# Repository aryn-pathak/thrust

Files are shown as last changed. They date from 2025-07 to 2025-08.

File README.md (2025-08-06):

# THRUST Freestyle drone and FC

## THRUST is an open source, sleek, lightweight, entry level FPV freestyle drone, powered by the custom THRUST FC made from scratch.

### THE THRUST MK1:

**A high speed drone, in a minimalistic yet striking frame, built for agility and a comfortable flying feel.**






### THE THRUST FC:

**Built to beat inaccesible, expensive, and capitalist FCs, at almost 1/6th the price of an average commercial FC, with the same perfomance, based on STM32F401CCU6, package of 40x31mm.**

Screenshot 2025-08-06 at 5 40 20 PM
Screenshot 2025-07-30 at 11 06 15 PM
Screenshot 2025-07-30 at 11 09 15 PM

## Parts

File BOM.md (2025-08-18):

# FC COMPONENTS

| Item | Price (INR) | Price (USD) |
| --- | --- | --- |
| [STM32F401CCU6](https://robu.in/product/stm32f401ccu6-stmicroelectronics-stm32f401ccu6-arm-mcu-dynamic-efficiency-line-stm32-family-stm32f4-series-microcontrollers-arm-cortex-m4/) | ₹495 | \$5.96 |
| [Switch (x2)](https://robu.in/product/tact-switch-tvcm15-5-2x5-2mm/) | ₹8 | \$0.10 |
| [Crystal](https://robu.in/product/hc-49smd-8mhz-20pf-20ppm-2pad-smd-smt-quartz-crystal-pack-of-2/) | ₹20 | \$0.24 |
| [AP2112K](https://robu.in/product/ap2112k-3-3trg1-diodes-inc-ldo-fixed-3-3v-0-6a-40-to-85deg-c/) | ₹29 | \$0.35 |
| [HC-12 (x2)](https://robu.in/product/hc-12-433-si4463-wireless-serial-module/) | ₹400 | \$4.82 |
| [Buck Module](https://robu.in/product/mini-mp1584-dc-dc-adjustable-buck-module-3a/) | ₹77 | \$0.93 |
| [USB Breakout](https://robu.in/product/usb-female-to-2-54mm-breakout-board-with-direct-4p-adapter-board/) | ₹13 | \$0.16 |
| Resistors & Capacitors | ₹40 | \$0.48 |
| [Inductor](https://robu.in/product/blm18kg101tn1d-murata-ferrite-beads-multi-layer-100ohm-25-100mhz-3a-0-03ohm-dcr-0603-t-r/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) | ₹3 | \$0.04 |
| PCB from JLCPCB (UPS Worldwide Express Saver) | ₹1398 | \$16 |
| **Total (FC Parts)** | **₹2483** | **\$39.04** |

# DRONE PARTS

| Item | Price (INR) | Price (USD)  |
| --- | --- | --- |
| [Propellers](https://robu.in/product/hurricane-mck-rev3-51366-3-pc-durable-mint-green/) | ₹224 | \$2.70 |
| [Dipole Antenna](https://robu.in/product/lwc-2400-dip-03-v1-0-dipole-antennas-2-4-ghz/) | ₹119 | \$1.43 |
| [Battery](https://robu.in/product/orange-11-1v-1800mah-3s-40c-lipo-battery-pack-xt60-connector/) | ₹1721 | \$20.73 |
| [ESCs (x4)](https://robu.in/product/simonk-30a-bldc-esc-electronic-speed-controller-without-connectors/) | ₹1380 | \$16.63 |
| [VTX](https://www.quadkart.in/akk-x2-ultimate-vtx/) | ₹2307 | \$27.79 |
| [Caddx Ant Lite](https://robu.in/product/caddx-ant-lite-analog-camera-fpv-cycle-edition-43/) | ₹1608 | \$19.37 |
| [Wire (1m) (x2)](https://roboticsdna.in/product/22-awg-high-quality-ultra-flexible-silicone-wire-1meter-black/) | ₹36 | \$0.43 |
| [1804-2480KV CCW Motor (x2)](https://robu.in/product/pro-range-d1804-2480kv-cww/) | ₹1280 | \$15.42 |
| [1804-2480KV CW Motor (x2)](https://robu.in/product/pro-range-d1804-2480kv-cw-brushless-drone-motor/) | ₹1280 | \$15.42 |
| [Battery Strap](https://robu.in/product/20cm-lipo-battery-strap-belt-reusable-cable-tie-wrap/) | ₹49 | \$0.59 |
| [Charger](https://robu.in/product/b3ac-compact-balance-charger-2s-3s-lipo/) | ₹337 | \$4.06 |
| [VRX (OTG Receiver)](https://robu.in/product/5-8g-uvc-otg-android-phone-receiver/) | ₹2429 | \$29.27 |
| [SMA to UFL](https://robu.in/product/lwc-ca-sma-jack-bh-st-ufl-1-13mm-rf-cable-assemblies-30cm/) | ₹79 | \$0.95 |
| **Total (Drone Components)** | **₹13,849** | **\$166.39** |

**SUBTOTAL DRONE+FC | 205.43**

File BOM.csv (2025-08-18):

Item | Price (INR) | Price (USD)
STM32F401CCU6 | ₹495 | $5.96
Switch (x2) | ₹8 | $0.10
Crystal | ₹20 | $0.24
AP2112K | ₹29 | $0.35
HC-12 (x2) | ₹400 | $4.82
Buck Module | ₹77 | $0.93
USB Breakout | ₹13 | $0.16
Resistors & Capacitors | ₹40 | $0.48
Inductor | ₹3 | $0.04
Propellers | ₹224 | $2.70
Dipole Antenna | ₹119 | $1.43
Battery | ₹1721 | $20.73
ESCs (x4) | ₹1380 | $16.63
VTX | ₹2307 | $27.79
Caddx Ant Lite | ₹1608 | $19.37
Wire (1m) (x2) | ₹36 | $0.43
1804-2480KV CCW Motor (x2) | ₹1280 | $15.42
1804-2480KV CW Motor (x2) | ₹1280 | $15.42
Battery Strap | ₹49 | $0.59
Charger | ₹337 | $4.06
VRX (OTG Receiver) | ₹2429 | $29.27
SMA to UFL | ₹79 | $0.95
PCB | ₹1397 | $16
**Total** | ₹16301 | $186.50

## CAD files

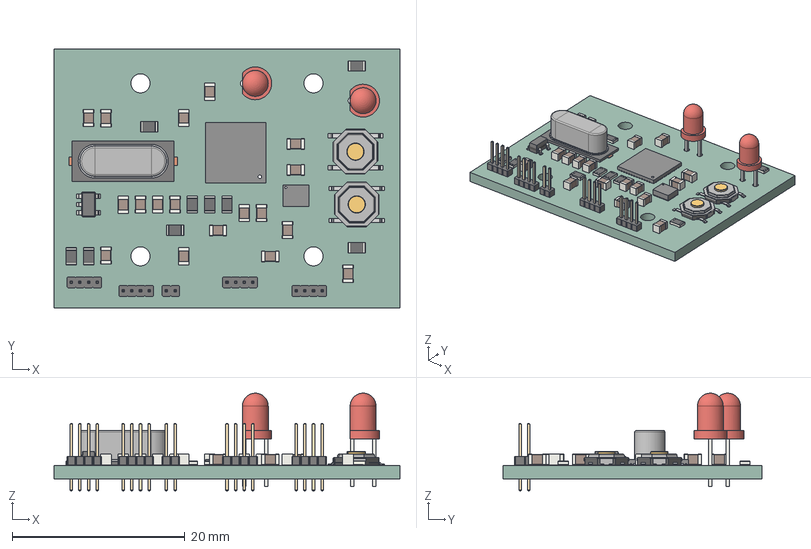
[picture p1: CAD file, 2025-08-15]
THRUST FC.step
40.0 x 30.0 x 11.3 mm
Crystal_SMD_HC49-SD
C_0805_2012Metric x 18
R_0805_2012Metric x 9
LED_D3.0mm x 2
PinHeader_1x04_P100mm_Vertical x 4
STM32U585CIU6Q
SW_SPST_TL3342 x 2
ICM-42688-P
PinHeader_1x02_P100mm_Vertical
SOT_23_5
THRUST FC_PCB

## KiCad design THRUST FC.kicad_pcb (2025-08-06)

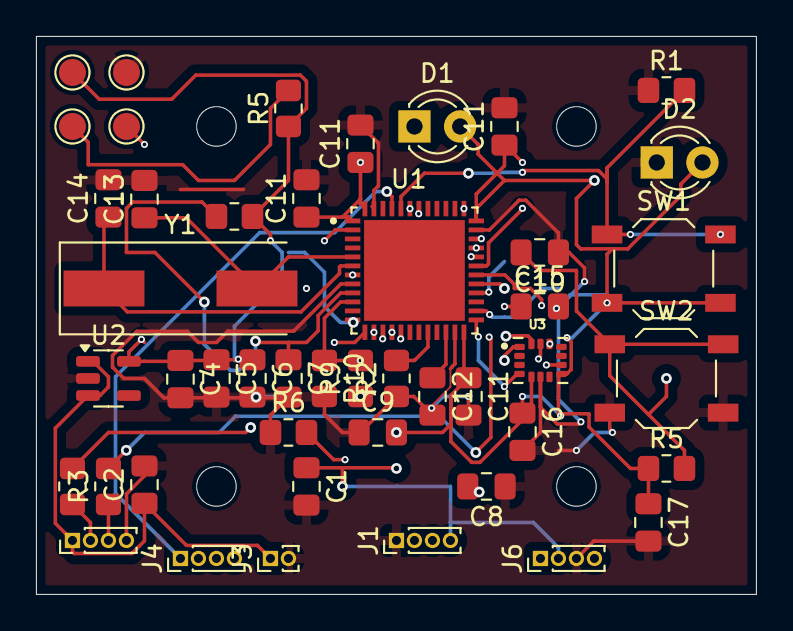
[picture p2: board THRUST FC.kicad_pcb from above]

Board: 4 copper layers, 40.0 x 31.0 mm, 42 parts (0 on the bottom side), 29 nets.

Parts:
C1, C6: 10 µF; C_0805_2012Metric_Pad1.18x1.45mm_HandSolder
C2: 10uF; C_0805_2012Metric_Pad1.18x1.45mm_HandSolder
C4, C8, C9, C10, C11, C11#2, C11#3, C11#4, C15, C16: 0.1 µF; C_0805_2012Metric_Pad1.18x1.45mm_HandSolder
C5, C7, C17: 1 µF; C_0805_2012Metric_Pad1.18x1.45mm_HandSolder
C12: 2.2µF; C_0805_2012Metric_Pad1.18x1.45mm_HandSolder
C13, C14: 18pF; C_0805_2012Metric_Pad1.18x1.45mm_HandSolder
D1, D2: LED; LED_D3.0mm
J1, J2, J6: Conn_01x04_Pin; PinHeader_1x04_P1.00mm_Vertical
J3: Conn_01x02_Pin; PinHeader_1x02_P1.00mm_Vertical
J4: ESC; PinHeader_1x04_P1.00mm_Vertical
L1: L; R_0805_2012Metric_Pad1.20x1.40mm_HandSolder
R1, R2, R5, R5#2, R6, R9, R10: 10k; R_0805_2012Metric_Pad1.20x1.40mm_HandSolder
R3, R4: 22; R_0805_2012Metric_Pad1.20x1.40mm_HandSolder
SW1, SW2: SW_Push; SW_SPST_TL3342
U1: STM32F401CCU6; QFN50P700X700X60-49N
U2: AP2112K-3.3; SOT-23-5
U3: ICM-42688-P; PQFN50P300X250X97-14N
Y1: Crystal; Crystal_SMD_HC49-SD

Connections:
+5V: C2.1, C8.2, J2.1, J3.1, R9.1, U2.1 (VIN), U2.3 (EN)
ADC: C15.1, R9.2, R10.1, U1.10 (PA0)
BOOT0: R1.2, SW1.1, U1.44 (BOOT0)
D+: J2.3, R3.1
D-: J2.2, R4.1
GND: C1.2, C2.2, C4.2, C5.2, C6.2, C7.2, C8.1, C9.1, C10.1, C11.2, C11#2.2, C11#3.2, C11#4.2, C12.2, C13.2, C14.2, C15.2, C16.2, C17.2, D2.1 (K), J1.1, J2.4, J3.2, J6.3, R1.1, R2.1, R6.1, R10.2, SW2.2, U1.8 (VSSA/VREF-), U1.23 (VSS), U1.35 (VSS), U1.47 (VSS), U2.2 (GND), U3.6 (GND)
M1: J4.4, U1.29 (PA8)
M2: J4.3, U1.30 (PA9)
M3: J4.2, U1.31 (PA10)
M4: J4.1, U1.45 (PB8)
NRST: C10.2, R5.2, SW2.1, U1.7 (~RST)
unnamed: C13.1, U1.5 (PH0-OSC_IN), Y1.2
unnamed: C14.1, U1.6 (PH1-OSC_OUT), Y1.1
unnamed: R6.2, U3.9 (INT2/FSYNC/CLKIN)
PA4: U1.14 (PA4), U3.12 (AP_CS)
PA5: U1.15 (PA5), U3.13 (AP_SCL/AP_SCLK)
PA6: U1.16 (PA6), U3.1 (AP_SDO/AP_AD0)
PA7: U1.17 (PA7), U3.14 (AP_SDA/AP_SDIO/AP_SDI)
PA11: R4.2, U1.32 (PA11)
PA12: R3.2, U1.33 (PA12)
PB2: R2.2, U1.20 (PB2)
PC13: D1.1 (K), U1.2 (PC13)
SCL: J6.1, U1.42 (PB6)
SDA: J6.4, U1.43 (PB7)
SWCLK: J1.2, U1.37 (PA14/JTCK-SWCLK)
SWDIO: J1.3, U1.34 (PA13/JTMS-SWDIO)
VCAP1: C12.1, U1.22 (VCAP_1)
VDD: C1.1, C4.1, C5.1, C6.1, C9.2, C11.1, C11#2.1, C11#3.1, C11#4.1, C16.1, C17.1, D1.2 (A), D2.2 (A), J1.4, J6.2, L1.2, R5.1, R5#2.1, SW1.2, U1.1 (VBAT), U1.24 (VDD), U1.36 (VDD), U1.48 (VDD), U2.5 (VOUT), U3.5 (VDDIO), U3.8 (VDD)
VREF+: C7.1, L1.1, U1.9 (VDDA/VREF+)

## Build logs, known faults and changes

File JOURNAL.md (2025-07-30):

---
title: "Thrust FPV stunt drone"
author: "aryan"
description: "a visually stunning FPV Stunt drone, with a custom FC"
created_at: "2025-06-23"
---

## TOTAL HOURS: 24

## DAY ONE

The drone should have the following qualities:
 - Small
 - agile (speed and quick turns)
 - have a custom FC
 - cameraaa
 - be resistant to crashes (or be designed to break in a way that it can be reassembled)
 - be under $150
 - look polished and visually striking (hoping to win highway design competition :3)
 - self stabilised

I also need to somehow make it in 3 days to be eligible for the competition :heavysob:, but i'm still gonna make it good

Today I'll start the flight controller PCB. I was confused between using STM32F4 chips (used most commonly in drones, great perfomance) and RP2040 (slower, but easier to setup). ChatGPT said STM32 chips are significantly harder to setup initially, but post talkuing to a few people on the slack, STM isn't too hard to setup, so I'll be using the [STM32F401CCU6](https://robu.in/product/stm32f401ccu6-stmicroelectronics-stm32f401ccu6-arm-mcu-dynamic-efficiency-line-stm32-family-stm32f4-series-microcontrollers-arm-cortex-m4/) with USB FS and STMDuino support.

## DAY TWO
Made most of the schematic today
Screenshot 2025-06-25 at 12 27 38 AM
This is mostly the low level stuff for the STM32 chip to work, and added ICM-42688-P. I'll be using an ESP32-CAM module for the camera and wireless connectivity. The camera is fully independent of the STM32, and a UART connection between ESP and STM32 is used for controls.

I don't think I'll be able to submit for the design competition :sob:, but that gives me more time to work on a well designed, high perfomance drone with a custom FC.

Tomorrow, I'll get started on BOM (battery, motors, ESCs, etc), and hopefully also finish the PCB!
### Schematic: 1.5 hours

## DAY THREE-FOUR
Worked more on the schematic, and finally finished it!
Screenshot 2025-06-29 at 12 38 36 AM

It's not exactly neat, but I'll organise and label the blocks later (when i ship it).

Also, a problem i realised when going to make the PCB-- I didn't label the capacitors' and resistors' capacitance and resistance respectively :skull:, so it'll take some more time.
### Schematic: 1.5-2 hours

## DAY FIVE
So I'm almost done with PCB layout, it's quite compact for now but i need to consider things like noise and interference with RF and MCU, so that might take another day.

PCB so far:

Screenshot 2025-07-09 at 9 41 33 PM

Rounting seemed VERY overwhelming till now, but it was done like a breeze lol
PCB: 1 hour

## DAY SIX
Okay, PCB is almost fully finished, just need to route the RF module and GND plane. (The entire PCB fits under 4.5cm?!)

Screenshot 2025-07-11 at 10 52 43 PM

This looks SO complicated but im really proud of myself for building this and not picking up a good expensive FC from a website :D

I wanted to work more but I also really need to start preparing for an upcoming MUN in a week

### PCB: 1.5 hours

## DAY SEVEN
I got to work after a looong time because of exams, and then an MUN i had to prepare for, so I will be locking in to make this now. Completed the PCB :D, however I need to face my biggest fear now (DRC :sob:). Also, while designing, i figured that if the ESP32-CAM was attached to the FC, it couldnt look at the surroundings, so I decided to just have +5V and GND test points to connect it using wires. 

### PCB: 1 hour

## DAY EIGHT

Today I started off with CAD, did some research and an unfortunate amount of time trying to understand mathematics of how a freestyle drone should be made, mostly looking at torque figure calculations. I was originally thinking of making a neat, aesthetic square-with-4-circles design. But after some research and looking at other designs, freestyle drones were almost exlusively of a shape called "streched X". This has something to do with moment of inertia and torque required to turn it. The pitch axis should have more t than the roll axis for a good, smooth, "gliding" like feel. The arms of the drone create 'r', which is the perpendicular distance of mass from the center, and t is directly proportional to it. It shouldnt be too less (for stability), but not too long (to not increase torque too much). Also, when I started, I started off with the ESP32-CAM module-- until I found an analog, high quality actual FPV camera. I had previously hugely underestimated the latency of WiFi.

I worked on several designs and arm shapes and none of them actually looked good/practical. I got very tired of constantly reiterating, drawing, deleting, extruding, tracing, moving, etc so I'll do it tomorrow.

### CAD, maths: 5-5.5 Hours

## DAY EIGHT
A good decision I made was watching a few build videos to understand how frames are made typically, which gave me a surprisingly good amount of understanding. Also found some components (cameras, ESC, VTX, etc). In the end, I settled on an "H-X Hybrid frame" (?) which I pretty much accidentally made. It co-incidentally looks similar to a deadcat frame too. A lot of CAD done, so I pretty much finalized it. Antenna mount, camera mount, screw holes, top, everything. I think it looks REALLY nice and unique. I plan on modifying the frame over the years as I get more knowledge and feel for freestyling drones; this is just MK1.



### CAD, shopping: 6 hours

## DAY NINE

The day I dreaded. DRC errors in such a complex PCB. Thankfully there weren't a LOT of hard-to-fix errors, but mostly about clearances and tracks not being connected to the STM32 (different layers), which was a CHALLENGE. it was so damn hard to reroute all the wires across 4 layers, try to fit a via somewhere without crossing lines :sob:. I also added 4 holes strategicaly to fit the ESC in a stack with the FC, which required me to reroute and reposition some components.

Screenshot 2025-07-30 at 9 18 44 PM
This image is the definition of "pain" :sob:

Anyways, it felt VERY good finally being done with the PCB-- finalized and fixed all DRC errors.
Screenshot 2025-07-30 at 9 24 42 PM
Screenshot 2025-07-30 at 9 25 28 PM

my beautiful beautiful son 🥹

### PCB: 2.5 hours

## DAY TEN
So the drone is pretty much done, just have to submit it now-- or so I thought. The BOM turned out to be ~7k INR more than the budget (💀), even though I only used reasonably priced components. Guess tomorrow will be for cutting costs :sob:

### Research and BOM: 2 hours

## DAY ELEVEN
Okay, so somehow I got the entire thing under the budget, using super cheap generic SimonK ESCs instead of the 4-in-1 ESC costing ~3k, replacing the holybro atlatl VTX with a cheaper VTX as well, and using a cheaper dipole antenna (since lollipop was overkill), and a significantly cheaper HC-12 RF module instead of the RFM69HCW. So haven't cut any functionality, maybe reduced ease of assembly and less beautiful, worth ~7k easily tho!

Submitting now! Massive thanks to hack club and the organisers of this YSWS-- its absolutely awesome!
### Documentation, BOM: 2.5-3 hours
